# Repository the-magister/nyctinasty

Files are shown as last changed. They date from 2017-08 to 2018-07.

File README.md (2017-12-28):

# Nyctinasty Oasis

Submitting for an Honoraria grant for Burning Man 2018.  An interactive playground celebrating the rhythm of night and day. By day the piece provides climbing fun, shade, and misters powered by movement. At night the lights come on, the sound enlivens and the fire and smoke show begins. The final night, the flower-like structure will wilt and burn.

3D render of Sepal

## Physical Description

Three climbable outriggers around a 32 ft radius circle surround a central flower. 16 ft tall, the outriggers support 20 people dancing and climbing. Built of wood and covered in shade cloth, they feature water misters and hammocks for daytime refuge. Misters are housed in vines, flowers decorate the structure, and leaf-like streamers unfurl overhead.

The center flower is a 16 ft tall metal structure comprised of three metal petals with flame and fog effect heads. Each petal is 3 ft W x 6ft L * 16 ft H. They each have a secured metal base, topped with a foldable rigid origami paneling crafted from 16 gauge metal with metal hinging. A propane accumulator is stored within each petal and plumbed to the tip of the paneling. Each base has 50 meters of RGB LEDs wrapped around the accumulator, diffused by semi-opaque HDPE panels.

## Interactivity and Mission

Nyctinasty Oasis is a day/night playground. Each outrigger is a climbable shade structure. With chill day music, participants can climb the structure, play with it to coax cooling mists, or take a break in the hammocks underneath.
Also incorporated is a sound puzzle, where the participants use movement to mix together multiple tracks of sounds to complete a song. Each outrigger contains three sensor bars which detect the frequency and location of the participants using infrared sensors. The game incorporates collaborative movement to create a coherent whole. Songs composed of three tracks (e.g., bass/melody/vocals) will have each track randomly assigned. As the dancers move and align their tracks, the lights and music will synchronize, rewarding with cooling mists and sounds during the day, and coordinated light at night.

The central flower coordinates with fire and fog. At the end of the week, Nyctinasty Oasis is burned, leaving participants to wonder if it was all a mirage.

## Philosophy

Nyctinasty is the circadian rhythmic movement of plants in response to day and night. An oasis is a fertile habitat found in a desert. Together, a nyctinasty oasis is a retreat that provides both respite and reactivity that changes and is available from day to night. We seek to express how experience varies depending on time of day, point of view, activity level, and community involvement. Nyctinasty Oasis has diurnal features that return upon sunrise and sundown, as well as constant features. During the day, Nyctinasty Oasis provides solace with shade, hammocks, and water misters. Chill, low-volume ambient music is controlled by interaction with the outrigger sensors. At night, the lights come out to play along with a multi-track interactive musical and fire experience that varies based on the number of participants at points along the outriggers. The Nyctinasty Oasis experience is externally guided by regular circadian elements, but also influenced by user participation and determination. The Nyctinasty Oasis also provides constants, a playground standing ready for climbing, hiding, and chilling day or night. We wish to communicate to participants that the experience will be regular, changeable, and replenishing.

## Hardware 

Nyctinasty functions as a distributed set of microcontrollers (uC).  In this sense, the project shares the archetecture of an IoT system.  However, processing is all conducted locally (as opposed to typical cloud-based IoT processing).

### Devices

* Networking: WiFi router, RFM69H(C)W peer-to-peer, FM for sound.
* Wemos D1 Mini (ESP8266): and mainstay microcontroller (uC).
* Arduino Nano (Atmel 328P): analog-to-digitial conversion
* Moteino R3 (Atmel 328P): bridge to legacy HopeRF-mediated peer-to-peer hardware
* Tsunami Super WAV Trigger (ARM Cortex m7): audio generation
* Sharp IR Distance Sensor (GP2Y0A02YK0F): range and motion detection
* Addressable LEDs (WS2811): lighting
* pump (TBD): mister system

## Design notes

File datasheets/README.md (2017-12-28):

Technical details for the devices used in the project.

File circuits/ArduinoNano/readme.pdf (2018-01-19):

### Arduino Nano V3.0 Module for CADSoft EAGLE

### This library was created by Esp. Marco-Luis SALCEDO TOVAR, please report any errors or suggestions to: yv1hx@cantv.net

This version: 0.6 (maintenance release), released on: January 01, 2.017.

### Revision history:

Version | Date | Comments
0.1 | January 22, 2.016 | Initial Release.
0.2 January 25, 2.016 | | Added: Revision history table. Updated: Minor cosmetic changes. Device general description.
0.3 February 05, 2.016 | | Added: Updated signal names labels on most multipurpose pins. Signal directions (Arrows) on D0/RX – D1/TX pins. Updated: Revision history table.
0.4 May 30, 2.016 | | Added: Center cross marks on board corner holes. Updated: Revision history table. Library updated and tested for compatibility on Eagle 7.5.0. Minor cosmetic changes on history table formatting. Updated device physical dimensions on general specifications table.
0.5 August 02, 2.016 | | Added: N/A. Updated: Revision history table. Library updated and tested for compatibility on Eagle 7.6.0.
0.6 January 01, 2.017 | | Added: N/A. Updated: Revision history table. Library updated and tested for compatibility on Eagle 7.7.0.

### Released under the Creative Commons Attribution-ShareAlike 2.5 Generic (CC

BY-SA 2.5) license terms.

### You are free to: Share — copy and redistribute the material in any medium or format Adapt — remix, transform, and build upon the material for any purpose, even

commercially.

### The licensor cannot revoke these freedoms as long as you follow the license

terms.
You can download a full copy of this license from here.

### Thanks for trying my library!

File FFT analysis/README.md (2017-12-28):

Processing the spacial-temporal data into frequency-temporal knowledge isn't trivial.  Each Arch has 8 distance sensors.  Each Sepal has three arches.  Nyctinasty has three Sepals.

From this, we can understand that processing distance data into "coordination" information is non-trivial!

Files in this area are stand-alone (R) applications that are used to develop methods.  Those methods, once sound, get translated to the uC code elsewhere.

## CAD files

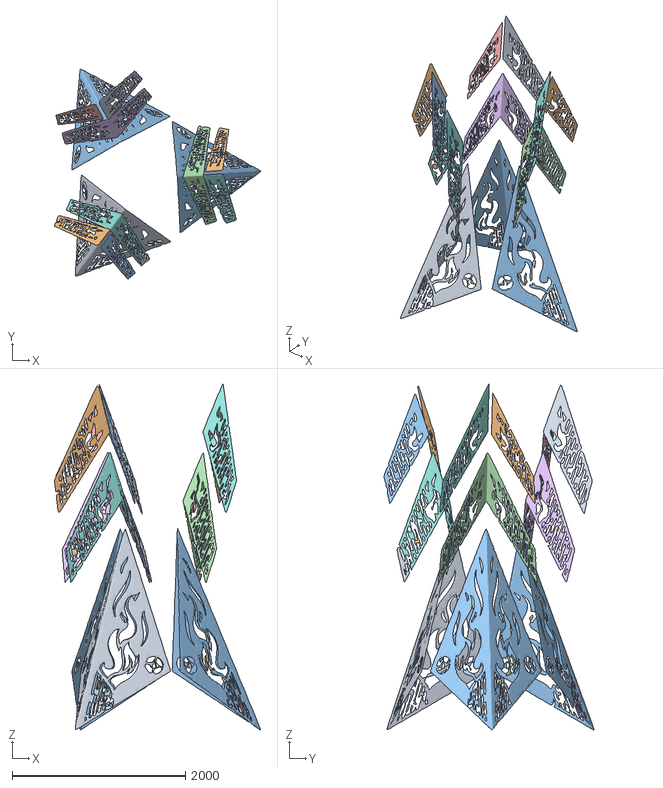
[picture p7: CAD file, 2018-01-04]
processing/sepal_status/application.linux-arm64/data/center - reduced.obj
2377.7 x 2424.0 x 3990.7

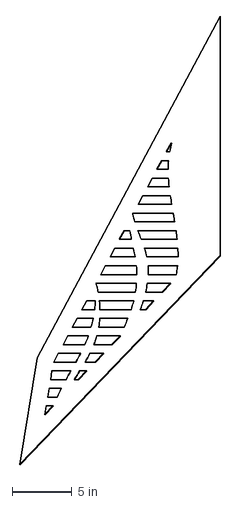
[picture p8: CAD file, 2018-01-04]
processing/sketch_sails/data/sail_A rev 3.DXF
16.8 x 37.6 in

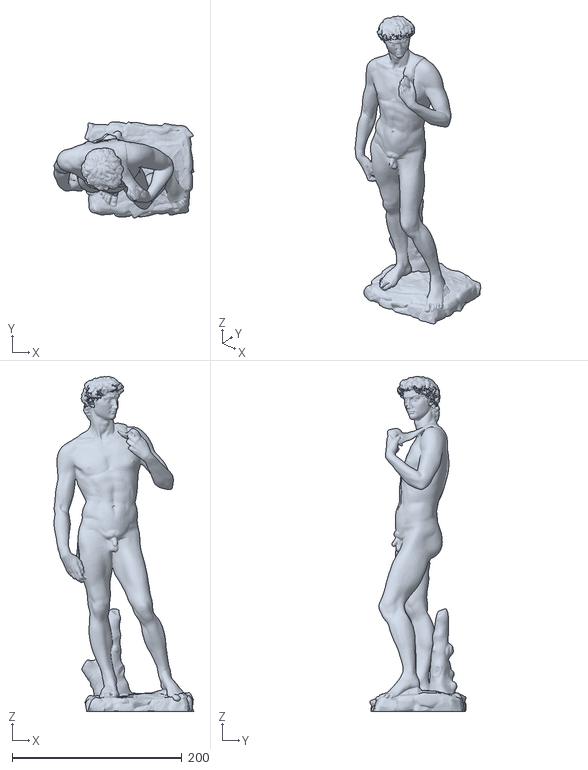
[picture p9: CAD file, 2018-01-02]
processing/sepal_status/application.linux-arm64/data/scan-the-world-michelangelo-s-david - reduced.obj
164.9 x 113.8 x 395.0

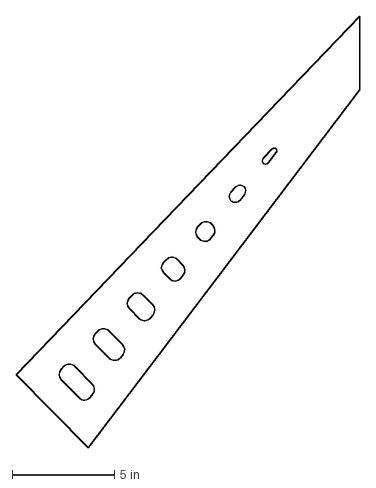
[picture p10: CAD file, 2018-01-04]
processing/sketch_sails/data/sail_B rev 3.DXF
16.8 x 21.1 in

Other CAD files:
processing/sketch_sails/data/sail_C rev 3.DXF
processing/sketch_sails/data/sail_G rev 3.DXF
processing/sketch_sails/data/sail_D rev 3.DXF
processing/sketch_sails/data/sail_E rev 3.DXF
processing/sketch_sails/data/sail_F rev 3.DXF
processing/sketch_sails/data/sail_F_v4.dxf

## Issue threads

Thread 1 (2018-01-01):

Router: bonjour/zeroconf services for OTA programming and *.local name resolution

the-magister, 2018-01-01:
Nyctinasty_Comms library module makes OTA programming via the IDE and name resolution in *.local available via mDNS.  The router is running avachi-daemon and mdns-daemon, so it should "see" the ESP8266 devices.  It doesn't, and I suspect:

- Something in dd-wrt is blocking that announcement/service.  I have tried turning off the firewall.
- Something in DNSmasq could be culprit for *.local lookup.

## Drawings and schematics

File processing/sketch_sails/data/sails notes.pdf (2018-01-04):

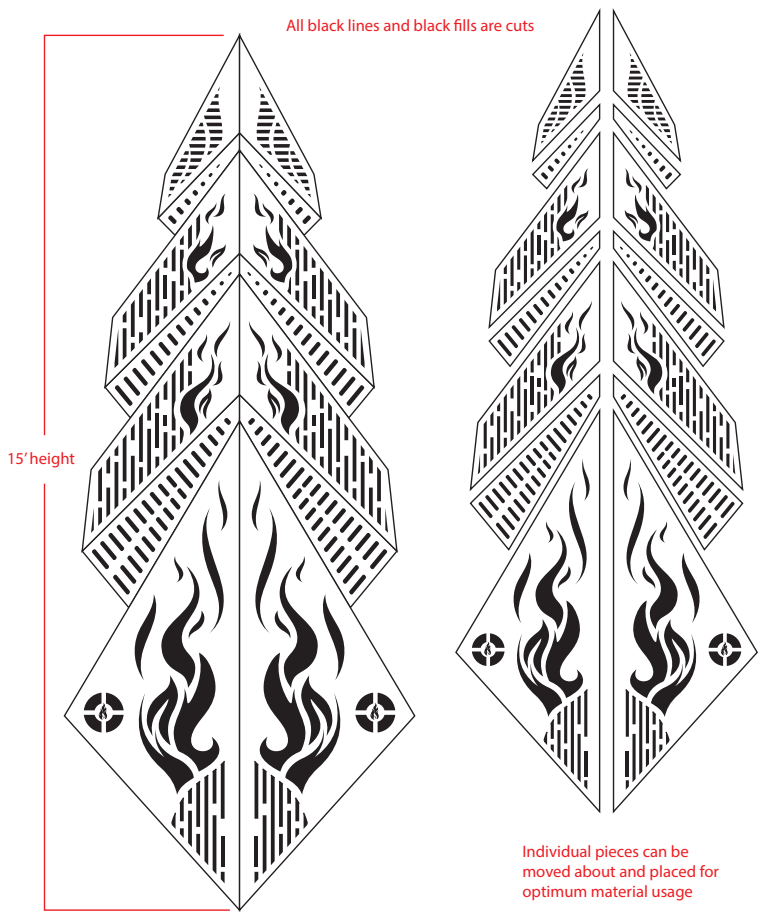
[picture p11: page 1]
15’ height

All black lines and black lls are cuts

Individual pieces can be
moved about and placed for
optimum material usage

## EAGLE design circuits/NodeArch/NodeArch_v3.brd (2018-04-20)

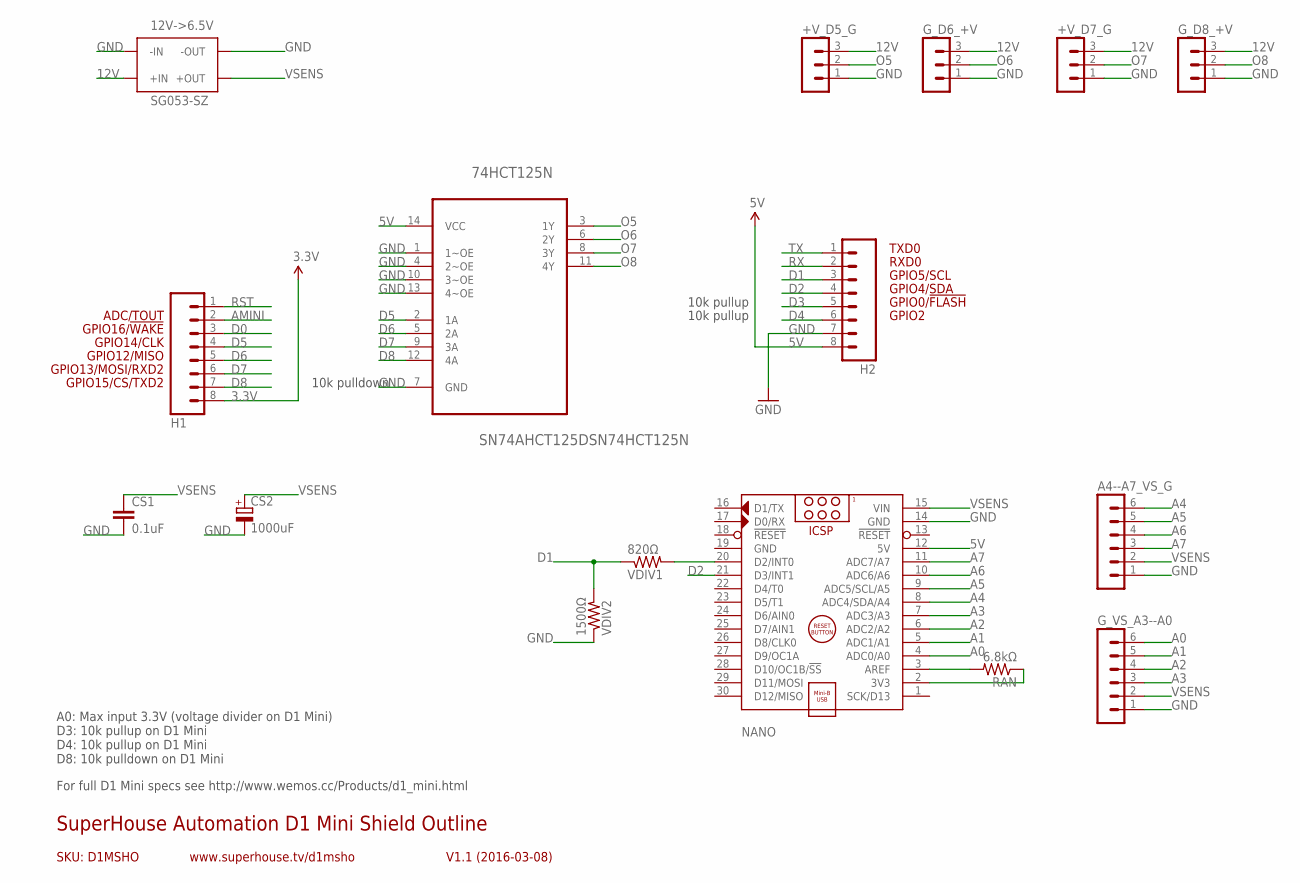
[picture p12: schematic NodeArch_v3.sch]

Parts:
12V->6.5V: SG053-SZ
74HCT125N: SN74AHCT125DSN74HCT125N; DIP254P762X508-14
+V_D5_G, +V_D7_G: MA03-1
A4--A7_VS_G: MA06-1
CS1: 0.1uF; C025-025X050
CS2: 1000uF; E5-10,5
G_D6_+V, G_D8_+V: MA03-1
G_VS_A3--A0: MA06-1
H1, H2: M08; 1X08
NANO: ARDUINO_NANO
RAN: 6.8kΩ; 0207/2V
VDIV1: 820Ω; 0207/2V
VDIV2: 1500Ω; 0207/2V

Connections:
3.3V: H1.8
5V: 74HCT125N.14 (VCC), H2.8, NANO.12 (5V)
12V: 12V->6.5V.P$3 (+IN), 12V->6.5V.P$4 (+IN), +V_D5_G.3, +V_D7_G.3, G_D6_+V.3, G_D8_+V.3
A0: G_VS_A3--A0.6, NANO.4 (ADC0/A0)
A1: G_VS_A3--A0.5, NANO.5 (ADC1/A1)
A2: G_VS_A3--A0.4, NANO.6 (ADC2/A2)
A3: G_VS_A3--A0.3, NANO.7 (ADC3/A3)
A4: A4--A7_VS_G.6, NANO.8 (ADC4/SDA/A4)
A5: A4--A7_VS_G.5, NANO.9 (ADC5/SCL/A5)
A6: A4--A7_VS_G.4, NANO.10 (ADC6/A6)
A7: A4--A7_VS_G.3, NANO.11 (ADC7/A7)
AMINI: H1.2
D0: H1.3
D1: H2.3, VDIV1.1, VDIV2.2
D2: H2.4, NANO.21 (D3/INT1)
D3: H2.5
D4: H2.6
D5: 74HCT125N.2 (1A), H1.4
D6: 74HCT125N.5 (2A), H1.5
D7: 74HCT125N.9 (3A), H1.6
D8: 74HCT125N.12 (4A), H1.7
GND: 12V->6.5V.P$1 (-IN), 12V->6.5V.P$2 (-IN), 12V->6.5V.P$7 (-OUT), 12V->6.5V.P$8 (-OUT), 74HCT125N.1 (1~OE), 74HCT125N.4 (2~OE), 74HCT125N.7 (GND), 74HCT125N.10 (3~OE), 74HCT125N.13 (4~OE), +V_D5_G.1, +V_D7_G.1, A4--A7_VS_G.1, CS1.2, CS2.-, G_D6_+V.1, G_D8_+V.1, G_VS_A3--A0.1, H2.7, NANO.14 (GND), NANO.19 (GND), VDIV2.1
unnamed: NANO.3 (AREF), RAN.2
unnamed: NANO.2 (3V3), RAN.1
unnamed: NANO.20 (D2/INT0), VDIV1.2
O5: 74HCT125N.3 (1Y), +V_D5_G.2
O6: 74HCT125N.6 (2Y), G_D6_+V.2
O7: 74HCT125N.8 (3Y), +V_D7_G.2
O8: 74HCT125N.11 (4Y), G_D8_+V.2
RST: H1.1
RX: H2.2
TX: H2.1
VSENS: 12V->6.5V.P$5 (+OUT), 12V->6.5V.P$6 (+OUT), A4--A7_VS_G.2, CS1.1, CS2.+, G_VS_A3--A0.2, NANO.15 (VIN)

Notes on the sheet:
GPIO2
GPIO0/!FLASH
GPIO12/MISO
GPIO4/SDA
GPIO5/SCL
RXD0
TXD0
GPIO13/MOSI/RXD2
GPIO14/CLK
GPIO15/CS/TXD2
GPIO16/!WAKE
SKU: D1MSHO
SuperHouse Automation D1 Mini Shield Outline
V1.1 (2016-03-08)
www.superhouse.tv/d1msho
ADC/TOUT
A0: Max input 3.3V (voltage divider on D1 Mini) D3: 10k pullup on D1 Mini D4: 10k pullup on D1 Mini D8: 10k pulldown on D1 Mini
10k pulldown
10k pullup
For full D1 Mini specs see http://www.wemos.cc/Products/d1_mini.html

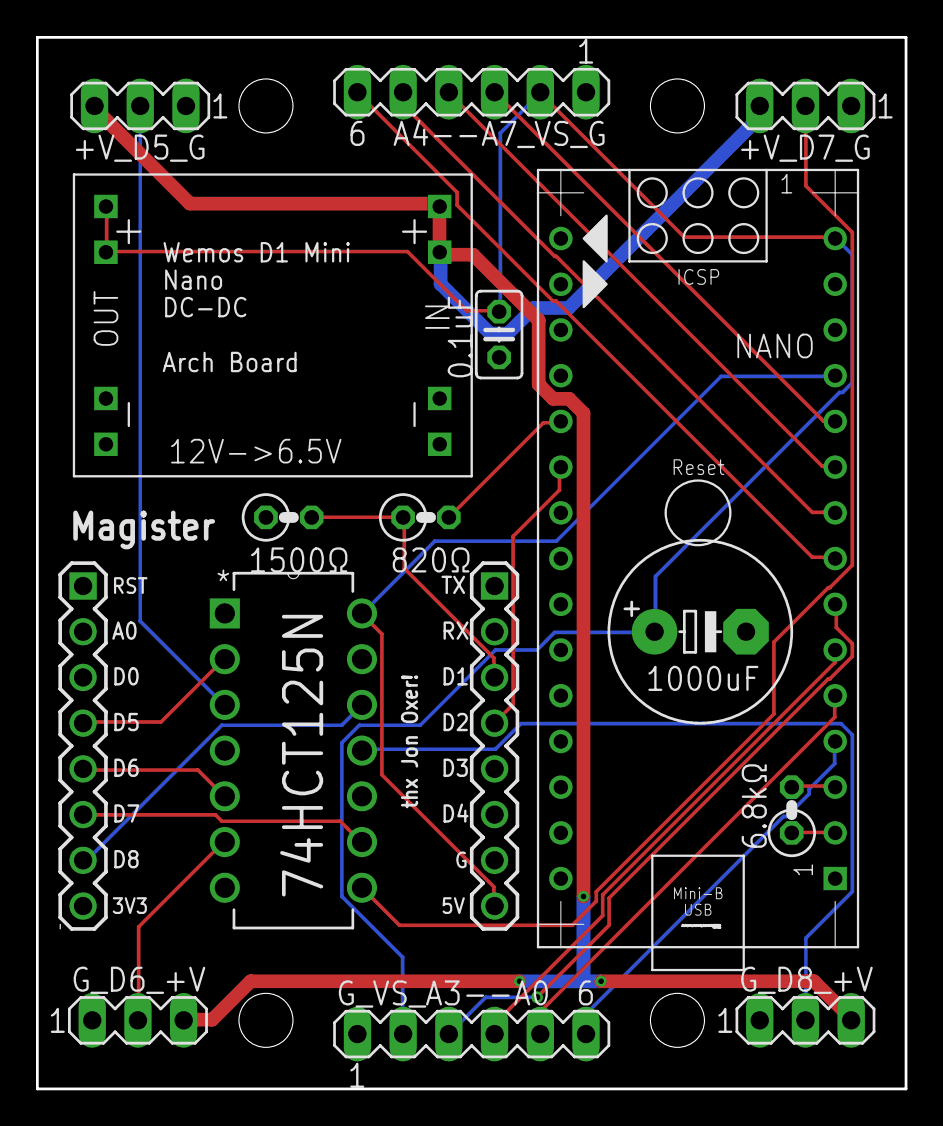
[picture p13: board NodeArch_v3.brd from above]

Board: 2 copper layers, 48.3 x 58.4 mm, 16 parts (0 on the bottom side), 25 nets.

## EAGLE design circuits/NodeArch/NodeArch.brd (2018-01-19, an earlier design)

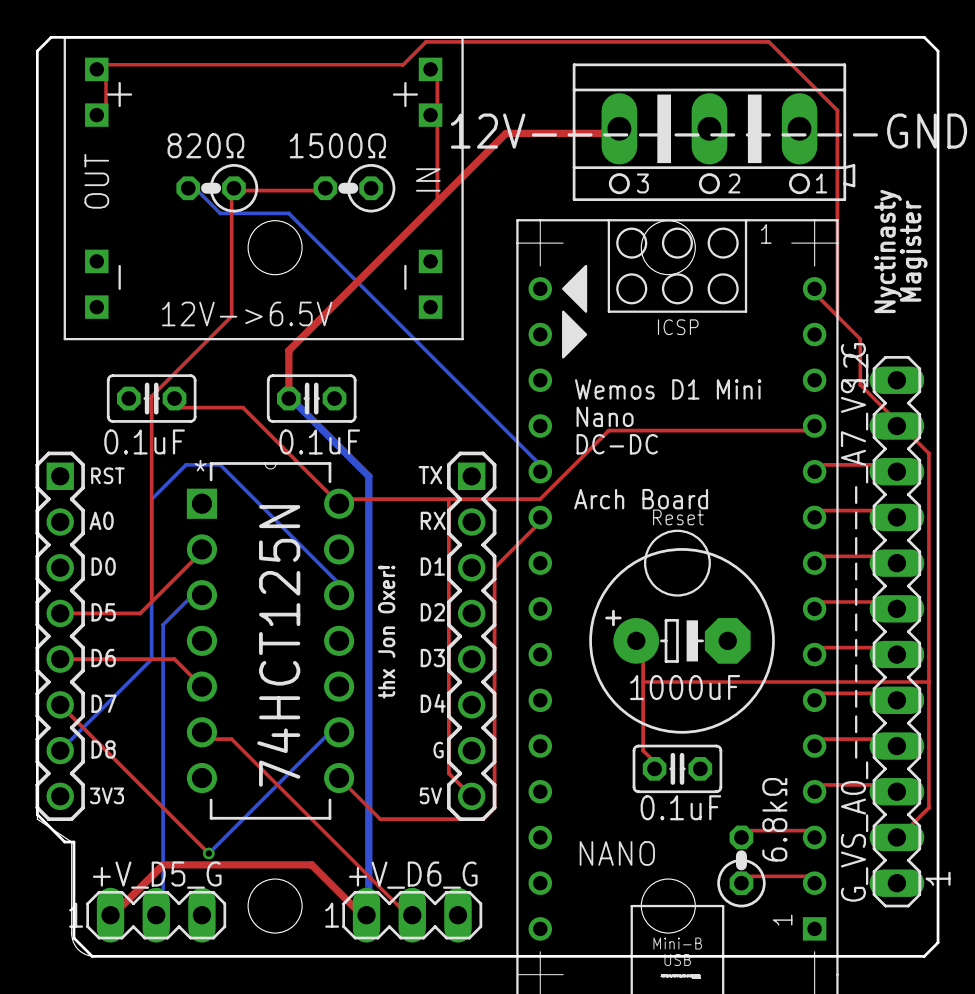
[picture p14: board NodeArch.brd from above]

Board: 2 copper layers, 50.0 x 51.1 mm, 16 parts (0 on the bottom side), 22 nets.

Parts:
12V----------GND: AK500/3
12V->6.5V: SG053-SZ
74HCT125N: SN74AHCT125DSN74HCT125N; DIP254P762X508-14
+V_D5_G, +V_D6_G: MA03-1
C5, C12: 0.1uF; C025-025X050
CS1: 0.1uF; C025-025X050
CS2: 1000uF; E5-10,5
G_VS_A0_-----------_A7_VS_G: MA12-1
H1, H2: 1X08
NANO: ARDUINO_NANO
RAN: 6.8kΩ; 0207/2V
VDIV1: 820Ω; 0207/2V
VDIV2: 1500Ω; 0207/2V

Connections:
5V: 74HCT125N.14, C5.1, H2.8, NANO.12
12V: 12V----------GND.3, 12V->6.5V.P$3, 12V->6.5V.P$4, +V_D5_G.1, +V_D6_G.1, C12.1
A0: G_VS_A0_-----------_A7_VS_G.3, NANO.4
A1: G_VS_A0_-----------_A7_VS_G.4, NANO.5
A2: G_VS_A0_-----------_A7_VS_G.5, NANO.6
A3: G_VS_A0_-----------_A7_VS_G.6, NANO.7
A4: G_VS_A0_-----------_A7_VS_G.7, NANO.8
A5: G_VS_A0_-----------_A7_VS_G.8, NANO.9
A6: G_VS_A0_-----------_A7_VS_G.9, NANO.10
A7: G_VS_A0_-----------_A7_VS_G.10, NANO.11
D5: 74HCT125N.2, H1.4, VDIV1.1, VDIV2.2
D6: 74HCT125N.5, H1.5
D7: 74HCT125N.9, H1.6
D8: 74HCT125N.12, H1.7
GND: 12V----------GND.1, 12V----------GND.2, 12V->6.5V.P$1, 12V->6.5V.P$2, 12V->6.5V.P$7, 12V->6.5V.P$8, 74HCT125N.1, 74HCT125N.4, 74HCT125N.7, 74HCT125N.10, 74HCT125N.13, +V_D5_G.3, +V_D6_G.3, C5.2, C12.2, CS1.2, CS2.-, G_VS_A0_-----------_A7_VS_G.1, G_VS_A0_-----------_A7_VS_G.12, H2.7, NANO.14, NANO.19, VDIV2.1
unnamed: NANO.3, RAN.2
unnamed: NANO.2, RAN.1
O5: 74HCT125N.3, +V_D5_G.2
O6: 74HCT125N.6, +V_D6_G.2
O7: 74HCT125N.8, NANO.21
TXAVR: NANO.20, VDIV1.2
VSENS: 12V->6.5V.P$5, 12V->6.5V.P$6, CS1.1, CS2.+, G_VS_A0_-----------_A7_VS_G.2, G_VS_A0_-----------_A7_VS_G.11, NANO.15

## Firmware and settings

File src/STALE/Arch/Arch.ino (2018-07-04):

// IDE Settings:
// Tools->Board : "WeMos D1 R2 & mini"
// Tools->Flash Size : "4M (3M SPIFFS)"
// Tools->CPU Frequency : "160 MHz"
// Tools->Upload Speed : "921600"

#include <Streaming.h>
#include <Metro.h>
#include <arduinoFFT.h>
#include <SoftwareSerial.h>
#include <SoftEasyTransfer.h>
#include <FiniteStateMachine.h>
#define FASTLED_INTERRUPT_RETRY_COUNT 1
#include <FastLED.h>
#include "Nyctinasty_Messages.h"
#include "Nyctinasty_Comms.h"

// spammy?
#define SHOW_SERIAL_DEBUG true

// my role and arch number
NyctRole myRole = N_ROLES; // see Nyctinasty_Comms.h; set N_ROLES to pull from EEPROM
// Arch0, Arch1, Arch2 for bootstrapping a new controller.
byte myArch;
byte leftArch, rightArch;
byte leftCoord, rightCoord;

// wire it up
#define RX D1 // GPIO5
#define TX D2 // GPIO4 
// voltage divider: 5V->3.3V
// TX to RX_ESP via 820 Ohm resistor
// RX_ESP to GND via 1500 Ohm resistor
// LEDs are connected:
// D5, GPIO14
// D6, GPIO12
// D7, GPIO13
// D8, GPIO15
// also used
// D4, GPIO2, BUILTIN_LED

// LED handling

// our internal storage, mapped to the hardware.
// pay no attention to the man behind the curtain.
#define COLOR_ORDER RGB
#define COLOR_CORRECTION TypicalLEDStrip
#define NUM_PINS 4
#define LEDS_BAR 3
#define LEDS_DOWN 17
#define LEDS_UP 13
#define LEDS_DECK 4
#define LEDS_PER_PIN LEDS_BAR+LEDS_DOWN

CRGBArray<LEDS_PER_PIN> leftBack;
CRGBArray<LEDS_PER_PIN> rightBack;
CRGBArray<LEDS_PER_PIN> leftFront;
CRGBArray<LEDS_PER_PIN> rightFront;

// bars
CRGBSet rightBar1 = rightBack(0, LEDS_BAR-1);
CRGBSet rightBar2 = rightFront(0, LEDS_BAR-1);
CRGBSet leftBar1 = leftBack(0, LEDS_BAR-1);
CRGBSet leftBar2 = leftFront(0, LEDS_BAR-1);

// verticals
CRGBSet leftUp = leftFront(LEDS_BAR, LEDS_UP-1);
CRGBSet rightUp = rightFront(LEDS_BAR, LEDS_UP-1);
CRGBSet leftDown = leftBack(LEDS_BAR, LEDS_DOWN-1);
CRGBSet rightDown = rightBack(LEDS_BAR, LEDS_DOWN-1);

// deck lights under rail
CRGBSet leftDeck = leftUp(LEDS_BAR+LEDS_UP, LEDS_PER_PIN-1);
CRGBSet rightDeck = rightUp(LEDS_BAR+LEDS_UP, LEDS_PER_PIN-1);

// color choices, based on arch information
const CHSV archColor[N_ARCH] = {
  CHSV(HUE_RED, 255, 255),
  CHSV(HUE_GREEN, 255, 255),
  CHSV(HUE_BLUE, 255, 255)
};

// deck lighting
CRGB deckColor = CRGB::FairyLight;

// comms
NyctComms comms;

// define a state for every systemState
void startup(); State Startup = State(startup);
void lonely(); State Lonely = State(lonely);
void ohai(); State Ohai = State(ohai);
void goodnuf(); State Goodnuf = State(goodnuf);
void goodjob(); State Goodjob = State(goodjob);
void winning(); State Winning = State(winning);
void fanfare(); State Fanfare = State(fanfare);
void reboot() { comms.reboot(); }; State Reboot = State(reboot);
FSM stateMachine = FSM(Startup); // initialize state machine

// incoming message storage and flag for update
struct sC_t {
  boolean hasUpdate = false;
  SystemCommand settings;
} sC;

// our distance updates send as this structure as this topic
const uint32_t distancePublishRate = 1000UL/15UL; // ms
SepalArchDistance dist;

// our frequency updates send as this structure as this topic
// other frequency updates receive as this structure as this topic
typedef struct {
  boolean hasUpdate = false;
  SepalArchFrequency freq;
} sAF_t;
sAF_t sAF[N_ARCH];

// FFT object
uint16_t buffer[N_SENSOR][N_FREQ_SAMPLES];
boolean bufferReady = false;
arduinoFFT FFT = arduinoFFT();

// computed correspondence [-1,+1] between arches.
float concordTotal, concordNext, concordPrev;

// talk to the ADC device
SoftwareSerial mySerial(RX, TX, false, 1024);
SoftEasyTransfer ETin;

void setup() {
  // for local output
  Serial.begin(115200);

  Serial << endl << endl << endl << F("Startup begins.") << endl;

  // for remote output
  Serial << F("Configure softwareserial...");
  mySerial.begin(115200);
  // messages
  ETin.begin(details(dist), &mySerial);
  // after set up the input pin
  pinMode(TX, OUTPUT); // trigger to send
  Serial << F(" done.") << endl;

  // LEDs
  Serial << F("Configure leds...");
  FastLED.addLeds<WS2811, D5, COLOR_ORDER>(leftBack, LEDS_PER_PIN).setCorrection(COLOR_CORRECTION);
  FastLED.addLeds<WS2811, D6, COLOR_ORDER>(rightBack, LEDS_PER_PIN).setCorrection(COLOR_CORRECTION);
  FastLED.addLeds<WS2811, D7, COLOR_ORDER>(leftFront, LEDS_PER_PIN).setCorrection(COLOR_CORRECTION);
  FastLED.addLeds<WS2811, D8, COLOR_ORDER>(rightFront, LEDS_PER_PIN).setCorrection(COLOR_CORRECTION);
  FastLED.setBrightness(255);
  Serial << F(" done.") << endl;

  // configure comms
  comms.begin(myRole);
  myRole = comms.getRole();
  myArch = myRole - 1;
  switch(myArch) {
    case 0: 
      // sC.isPlayer indexes
      leftArch=1; rightArch=2; 
      // sC.areCoordinated indexes
      leftCoord=0; rightCoord=2;
      break;
    case 1: 
      leftArch=2; rightArch=0; 
      leftCoord=1; rightCoord=0;
      break;
    case 2: 
      leftArch=0; rightArch=1; 
      leftCoord=2; rightCoord=1;
      break;    
  }
  Serial << F("Arch indexes: left=") << leftArch << F(" my=") << myArch << F(" right=") << rightArch << endl;
  Serial << F("Coordination indexes: left=") << leftCoord << F(" right=") << rightCoord << endl;
  
  // subscribe
  comms.subscribe(&sC.settings, &sC.hasUpdate);
  for ( byte a = 0; a < N_ARCH; a++ ) {
    // no need to subscribe to our own message
    if ( a != myArch ) comms.subscribe(&sAF[a].freq, &sAF[a].hasUpdate, a);
  }

  Serial << F("DISTANCE_SAMPLING_RATE, ms: ") << DISTANCE_SAMPLING_RATE << endl;
  Serial << F("DISTANCE_SAMPLING_FREQ, Hz: ") << DISTANCE_SAMPLING_FREQ << endl;
  Serial << F("N_FREQ_SAMPLES, #: ") << N_FREQ_SAMPLES << endl;
  Serial << F("FILL_TIME, ms: ") << FILL_TIME << endl;
  Serial << F("Lowest Freq Bin, Hz: ") << (float)(0+1)*(float)DISTANCE_SAMPLING_FREQ/(float)N_FREQ_SAMPLES << endl;
  Serial << F("Highest Freq Bin, Hz: ") << (float)(N_FREQ_BINS+1)*(float)DISTANCE_SAMPLING_FREQ/(float)N_FREQ_SAMPLES << endl;

  Serial << F("Startup complete.") << endl;
}

void loop() {
  // comms handling
  comms.update();

/*
  // after 5 seconds, transition to Offline, but we could easily get directed to Online before that.
  static Metro cycleTimeout(5000UL);
  if( cycleTimeout.check() ) {
    sC.settings.state = (systemState)((int)sC.settings.state+1);
    if( sC.settings.state == REBOOT ) sC.settings.state = STARTUP;
    sC.hasUpdate = true;
    cycleTimeout.reset();
  }
*/

  // check for settings update
  if ( sC.hasUpdate ) {
    updateState();
    calculateCoordPalette();
    calculatePlayerPalette();
    sC.hasUpdate = false;
  }

  // do stuff
  stateMachine.update();

  // update the sensor data
  updateSensors();
}

CRGBPalette16 coordPalette;
void calculateCoordPalette() {
  
  CRGBArray<16> pal;
  
  if( sC.settings.areCoordinated[leftCoord] ) {
    pal.fill_gradient(archColor[leftArch], archColor[myArch], archColor[leftArch] );
  } else {
    pal = CRGB::Black;
  }
  if( sC.settings.areCoordinated[rightCoord] ) {
    pal.fill_gradient(archColor[rightArch], archColor[myArch], archColor[rightArch] );
  } else {
    pal = CRGB::Black;
  }

  // copy out
  for(byte i=0; i<16; i++) coordPalette[i] = pal[i];
}

CRGBPalette16 playerPaletteLeft, playerPaletteRight; // left, right
void calculatePlayerPalette() {
  
  CHSV me = CHSV(archColor[myArch].hue, archColor[myArch].sat, 
    sC.settings.isPlayer[myArch] ? 255 : 0
  );
  CHSV left = CHSV(archColor[leftArch].hue, archColor[leftArch].sat, 
    sC.settings.isPlayer[leftArch] ? 255 : 0
  );
  CHSV right = CHSV(archColor[rightArch].hue, archColor[rightArch].sat, 
    sC.settings.isPlayer[rightArch] ? 255 : 0
  );

  CRGBArray<16> palLeft;
  palLeft.fill_gradient(left, me, left);

  CRGBArray<16> palRight;
  palRight.fill_gradient(right, me, right);
 
  // copy out
  for(byte i=0; i<16; i++) {
    playerPaletteLeft[i] = palLeft[i];
    playerPaletteRight[i] = palRight[i];
  }
}


void updateState() {

  switch ( sC.settings.state ) {
    case STARTUP: stateMachine.transitionTo(Startup); break;
    case LONELY: stateMachine.transitionTo(Lonely); break;
    case OHAI: stateMachine.transitionTo(Ohai); break;
    case GOODNUF: stateMachine.transitionTo(Goodnuf); break;
    case GOODJOB: stateMachine.transitionTo(Goodjob); break;
    case WINNING: stateMachine.transitionTo(Winning); break;
    case FANFARE: stateMachine.transitionTo(Fanfare); break;
    case REBOOT: stateMachine.transitionTo(Reboot); break;
    default:
      Serial << F("ERROR!  unknown state.") << endl;
  }

  Serial << F("State change. to=");
  switch( sC.settings.state ) {
    case STARTUP: Serial << "STARTUP"; break;  //  all roles start here
  
    case LONELY: Serial << "LONELY"; break;   // 0 players
    case OHAI: Serial << "OHAI"; break;   // 1 players
    case GOODNUF: Serial << "GOODNUF"; break;  // 2 players
    case GOODJOB: Serial << "GOODJOB"; break;  // 3 players or 2 players coordinated
    case WINNING: Serial << "WINNING"; break;  // 3 players and 2 players coordinated
    case FANFARE: Serial << "FANFARE"; break;  // 3 players and 3 players coordinated 
  
    case REBOOT: Serial << "REBOOT"; break;   //  trigger to reboot 
  }
  Serial << ". isPlayer? A0=" << sC.settings.isPlayer[0];
  Serial << " A1=" << sC.settings.isPlayer[1];
  Serial << " A2=" << sC.settings.isPlayer[2];
  Serial << ". coord? A01=" << sC.settings.areCoordinated[0];
  Serial << " A12=" << sC.settings.areCoordinated[1];
  Serial << " A20=" << sC.settings.areCoordinated[2];
  Serial << endl;

}

void startup() {
  
  static byte hue = archColor[myArch].hue;
  EVERY_N_MILLISECONDS(10) {
    // show a throbbing rainbow background
    hue++;
    leftUp.fill_rainbow(hue, 255 / leftUp.size()); // paint
    rightUp = leftUp;
    leftDown.fill_rainbow(hue + 128, -255 / leftDown.size());
    rightDown = leftFront;
    
    // color the bar with our color
    leftBar1.fill_solid(archColor[myArch]);
    rightBar2 = rightBar1 = leftBar2 = leftBar1;
    
    // do it now
    pushToHardware();
  }

}

void lonely() {
  // need some kind of "walk into the arches" animation
  playerAndCoordinationUpdate();
}

void ohai() {
  playerAndCoordinationUpdate();
}

void goodnuf() {
  playerAndCoordinationUpdate();
}

void goodjob() {
  playerAndCoordinationUpdate();
}

void winning() {
  playerAndCoordinationUpdate();
}

void fanfare() {
  // need some kind of "yeah, playah!" animation
  playerAndCoordinationUpdate();
}

void playerAndCoordinationUpdate() {
  updateDeck();
  updateTopsByCoordination();
  updateLegsByPlayer();
}

void updateDeck() {
  leftDeck.fill_solid(deckColor);
  rightDeck.fill_solid(deckColor);
}

void updateTopsByCoordination() {
  static byte colorIndex = 0;  
  
  EVERY_N_MILLISECONDS( 20 ) {
    colorIndex ++;
    byte j = 0;
    for ( int i = 0; i < leftUp.size(); i++) {
      leftUp[i] = ColorFromPalette( coordPalette, colorIndex + j++, 255, LINEARBLEND );
    }
    j = 0;
    for ( int i = 0; i < rightUp.size(); i++) {
      rightUp[i] = ColorFromPalette( coordPalette, colorIndex + j++, 255, LINEARBLEND );
    }
  }  
}

void updateLegsByPlayer() {
  static byte colorIndex = 0;
  
  EVERY_N_MILLISECONDS( 20 ) {
    colorIndex ++;
    byte j = 0;
    for ( int i = 0; i < leftDown.size(); i++) {
      leftDown[i] = ColorFromPalette( playerPaletteLeft, colorIndex + j++, 255, LINEARBLEND );
    }
    j = 0;
    for ( int i = 0; i < rightDown.size(); i++) {
      rightDown[i] = ColorFromPalette( playerPaletteRight, colorIndex + j++, 255, LINEARBLEND );
    }
  }  

}

void updateSensors() {

/*
 * Order of operation is critical here.  We have three subsystems that use ISRs:
 *  FastLED: turns off ISRs
 *  WiFi: received information may be lost w/o ISR
 *  SoftwareSerial: received information may be lost w/o ISR
 *  
 *  From this, you can see that we need to be very careful with FastLED.show(), and 
 *  queue those up after we get SoftwareSerial data.  Can't really control when we get
 *  WiFi packets.
 *
 */
 
 static uint32_t counter = 0;
  static boolean publishReady = false;
  static byte fftIndex = 0;
  static Metro pushDistanceInterval(distancePublishRate);

  // do FFT in segements when the buffer is ready
  if ( bufferReady ) {
    // compute
    computeFFT(fftIndex);

    // next sensor
    fftIndex++;

    // are we done?
    if ( fftIndex >= N_SENSOR ) {
      fftIndex = 0;
      bufferReady = false;
      publishReady = true;
    }
  }

  // check to see if we need to pull new distance data.
  // toggled TX pin
  static boolean pinState = false;
  static Metro distanceUpdate(DISTANCE_SAMPLING_RATE);

  if ( distanceUpdate.check() ) {
    distanceUpdate.reset();
    pinState = !pinState;
    digitalWrite(TX, pinState);
  }

  // get data from ADCs
  if ( ETin.receiveData() ) {
    // just tracking actual distance update rate
    counter ++;

    // fill buffer
    fillBuffer();

    // update bar lights
    updateBarByDistance();

    // I don't actually know if sending via WiFi will disrupt SoftwareSerial; worth a look.
    if ( publishReady ) {
      publishReady = false;
      // publish
      comms.publish(&sAF[myArch].freq, myArch);
      // flag that our frequency data are ready
      sAF[myArch].hasUpdate = true;
    } else if( pushDistanceInterval.check() ) {
      // publish distance
      comms.publish(&dist, myArch);
      pushDistanceInterval.reset();
    }

    // we need to update the LEDs now while we won't screw up SoftwareSerial and WiFi
    pushToHardware();
  }

  const uint32_t reportInterval = 10;
  EVERY_N_SECONDS( reportInterval ) {
    uint32_t actualDISTANCE_SAMPLING_RATE = (reportInterval*1000UL)/counter;

    Serial << F("Distance sample interval, actual=") << actualDISTANCE_SAMPLING_RATE;
    Serial << F(" hypothetical=") << DISTANCE_SAMPLING_RATE;
    Serial << F(" ms.") << endl;
    
    counter=0;
  }
  
}

// adjust lights on the bar with distance readings
void updateBarByDistance() {

  // compute using a dummy set of LEDs
  static CRGBArray<N_SENSOR> bar;
  for ( byte s = 0; s < N_SENSOR; s++ ) {
    // quash noise
    if ( dist.prox[s] < dist.noise ) dist.prox[s] = dist.min;
    uint16_t intensity = map(
                           dist.prox[s],
                           dist.min, dist.max,
                           (uint16_t)0, (uint16_t)255
                         );
    bar[s] = CHSV(archColor[myArch].hue, archColor[myArch].sat, (byte)intensity);
  }

  // assign to hardware. ugly and direct, but we can see what's going on.
  leftBack[2] = leftFront[2] = bar[0];
  leftBack[1] = leftFront[1] = bar[1];
  leftBack[0] = leftFront[0] = bar[2];

  rightBack[0] = rightFront[0] = bar[3];
  rightBack[1] = rightFront[1] = bar[4];
  rightBack[2] = rightFront[2] = bar[5];
}

// adjust lights on the down/legs with frequency readings
void updateLegsByFrequency() {
  // crappy
  uint16_t avgPower[N_SENSOR] = {0};
  // frequency power
  uint16_t power[N_SENSOR][N_FREQ_BINS] = {{0.0}};

  // do the boneheaded thing and sum up the bins across all sensors
  uint32_t sumSensors[N_FREQ_BINS] = {0};
  uint32_t maxSum = 0;
  for ( uint16_t b = 0; b < N_FREQ_BINS ; b++ ) {
    for ( byte s = 0; s < N_SENSOR; s++ ) {
      sumSensors[b] += sAF[myArch].freq.power[s][b];
    }
    if ( sumSensors[b] > maxSum ) maxSum = sumSensors[b];
  }

  Serial << F("Freq bins: ");
  // set the LEDs proportional to bins, normalized to maximum bin
  for ( uint16_t b = 0; b < N_FREQ_BINS ; b++ ) {
    uint32_t value = map( sumSensors[b],
                          (uint32_t)0, maxSum,
                          (uint32_t)0, (uint32_t)255
                        );
    Serial << value << ",";
    leftDown[b] = CHSV(archColor[myArch].hue, archColor[myArch].sat, brighten8_video(constrain(value, 0, 255)));
  }
  Serial << endl;

  rightDown = leftDown;
}

// adjust lights on down/legs with peak frequency readings
void updateLegsByPeakFreq() {

  // some constants
  // maximum possible frequency bin
  const byte maxFreq = ceil( (N_FREQ_BINS+1)*DISTANCE_SAMPLING_FREQ/N_FREQ_SAMPLES );
  const byte minFreq = floor( (0+1)*DISTANCE_SAMPLING_FREQ/N_FREQ_SAMPLES );
  const byte fadeEachUpdate = 128;
  
  // fade lighting
  leftDown.fadeToBlackBy( fadeEachUpdate );

  // loop across each arch's information
  for( byte a=0; a<N_ARCH; a++ ) {
    // loop across each sensor
    for( byte s=0; s<N_SENSOR; s++ ) {
      // get the integer frequency above and below
      byte roundUp = ceil(sAF[a].freq.peakFreq[s]);
      byte roundDown = floor(sAF[a].freq.peakFreq[s]);
      
      // map to lighting position
      byte lightUp = map(roundUp, minFreq, maxFreq, 0, LEDS_UP-1);
      byte lightDown = map(roundDown, minFreq, maxFreq, 0, LEDS_DOWN-1);
      
      // pick a color; my color is the brightest.
      byte bright = 128;
      if( a == myArch ) bright = 255;
      CHSV color = CHSV(archColor[a].hue, 255, bright );

      // apply
      leftDown[lightUp] += color;
      leftDown[lightDown] += color;
    }
    
  }

  // What immortal hand or eye / Could frame thy fearful symmetry?
  rightDown = leftDown;
}

// update lights on the up/overhead with concordance readings
void updateTopsByConcordance() {
  // NOP
}

// show
void pushToHardware() {
  FastLED.show();

  // show our frame rate, periodically
  EVERY_N_SECONDS( 20 ) {
    uint16_t reportedFPS = FastLED.getFPS();
    Serial << F("FastLED reported FPS, Hz=") << reportedFPS << endl;
  }
}

// storage
void fillBuffer() {
  // track the buffer index
  static uint16_t index = 0;

  // push to buffer
  for ( byte i = 0; i < N_SENSOR; i++ ) buffer[i][index] = dist.prox[i];

  // increment buffer index
  index++;

  if ( index >= N_FREQ_SAMPLES ) {
    index = 0;
    bufferReady = true;
  }
}

// show sensor readings
void dumpBuffer(uint16_t count) {
  const char sep = ',';

  for ( uint16_t j = 0; j < N_FREQ_SAMPLES; j++) {
    for ( uint16_t i = 0; i < N_SENSOR; i++ ) {
      Serial << (uint16_t)buffer[i][j] << sep;
    }
    Serial << count << endl;
  }
  count ++;
}

// frequency calculations readings
void dumpFFT() {
  const char sep = ',';
  unsigned long now = millis();

  for ( uint16_t i = 0; i < N_SENSOR; i++ ) {
    Serial << now << sep << i << sep << sAF[myArch].freq.avgPower[i];
    for ( uint16_t j = 0; j < N_FREQ_BINS ; j++ ) {
      Serial << sep << sAF[myArch].freq.power[i][j];
    }
    Serial << endl;
  }
}


// https://cdn-learn.adafruit.com/downloads/pdf/fft-fun-with-fourier-transforms.pdf
// Nyquist's Sampling Theorem: only frequencies up to half the sampling rate can
// can be detected.  So, for 33 fps (Hz) we can detect signals no faster than 33/2 Hz.
/*
  Finally, the output of the FFT on real data has a few interesting properties:
    The very first bin (bin zero) of the FFT output represents the average power of the signal.
  Be careful not to try interpreting this bin as an actual frequency value!
   Only the first half of the output bins represent usable frequency values. This means the
  range of the output frequencies detected by the FFT is half of the sample rate. Don't try to
  interpret bins beyond the first half in the FFT output as they won't represent real frequency
  values!
*/
double imag[N_FREQ_SAMPLES];
double real[N_FREQ_SAMPLES];
#define SCL_INDEX 0x00
#define SCL_TIME 0x01
#define SCL_FREQUENCY 0x02
void computeFFT(byte index) {
  // track time
  unsigned long tic = millis();

  // crunch the buffer; expensive
  const uint8_t exponent = FFT.Exponent(N_FREQ_SAMPLES); // can precompute to save a little time.

  // storage.  fft computations alter the buffer, so we copy
  for ( uint16_t j = 0; j < N_FREQ_SAMPLES ; j++ ) {
    real[j] = (double)buffer[index][j];
    imag[j] = 0.0;
  }

  // weigh data
  FFT.Windowing(real, N_FREQ_SAMPLES, FFT_WIN_TYP_HAMMING, FFT_FORWARD);  /* Weigh data */
  //    Serial.println("Weighed data:"); PrintVector(real, N_FREQ_SAMPLES, SCL_TIME);

  // compute FFT
  FFT.Compute(real, imag, N_FREQ_SAMPLES, exponent, FFT_FORWARD); /* Compute FFT */
  //    Serial.println("Computed Real values:"); PrintVector(real, N_FREQ_SAMPLES, SCL_INDEX);
  //    Serial.println("Computed Imaginary values:"); PrintVector(imag, N_FREQ_SAMPLES, SCL_INDEX);

  // compute magnitudes
//  FFT.ComplexToMagnitude(real, imag, N_FREQ_SAMPLES); /* Compute magnitudes */
  // stealing a march here, as we don't need the magnitude information for the latter
  // half of the array
  FFT.ComplexToMagnitude(real, imag, N_FREQ_BINS + 2); /* Compute magnitudes */
//  Serial.println("Computed magnitudes:");  PrintVector(real, (N_FREQ_SAMPLES >> 1), SCL_FREQUENCY);

  // find major frequency peak
  double peakFreq = FFT.MajorPeak(real, N_FREQ_SAMPLES, DISTANCE_SAMPLING_FREQ);
//  if( index==5 ) Serial << F("Peak: ") << x << endl;
  
  // store power magnitudes of the lowest N_FREQ_BINS in the spectra
  sAF[myArch].freq.avgPower[index] = (uint16_t)real[0];
  for ( uint16_t j = 0; j < N_FREQ_BINS ; j++ ) sAF[myArch].freq.power[index][j] = (uint16_t)real[j + 1];

  // store peak frequency
  sAF[myArch].freq.peakFreq[index] = (float)peakFreq;
  
/*
  unsigned long dur = (millis() - tic);
  if ( index == 0 ) {
    Serial << F("Last FFT complete.");
    Serial << F(" duration=") << dur;
    Serial << F(" ms.") << endl;
  }
  */
}
void PrintVector(double *vData, uint16_t bufferSize, uint8_t scaleType) {
  for (uint16_t i = 0; i < bufferSize; i++)   {
    double abscissa;
    /* Print abscissa value */
    switch (scaleType)
    {
      case SCL_INDEX:
        abscissa = (i * 1.0);
        break;
      case SCL_TIME:
        abscissa = ((i * 1.0) / DISTANCE_SAMPLING_FREQ);
        break;
      case SCL_FREQUENCY:
        abscissa = ((i * 1.0 * DISTANCE_SAMPLING_FREQ) / (double)N_FREQ_SAMPLES);
        break;
    }
    Serial.print(abscissa, 6);
    Serial.print(" ");
    Serial.print(vData[i], 4);
    Serial.println();

    // Only the first half of the output bins represent usable frequency values.
    if ( scaleType == SCL_FREQUENCY && i >= (bufferSize / 2 - 1) ) return;
  }
  Serial.println();
}
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

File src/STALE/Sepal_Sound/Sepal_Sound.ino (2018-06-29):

// IDE Settings:
// Tools->Board : "WeMos D1 R2 & mini"
// Tools->Flash Size : "4M (3M SPIFFS)"
// Tools->CPU Frequency : "160 MHz"
// Tools->Upload Speed : "921600"

#include <Streaming.h>
#include <Metro.h>
#include <SoftwareSerial.h>
#include <FiniteStateMachine.h>
#include <Tsunami.h>
#include "Nyctinasty_Messages.h"
#include "Nyctinasty_Comms.h"

// spammy?
#define SHOW_SERIAL_DEBUG true

// my role and arch number
NyctRole myRole = Sound; // see Nyctinasty_Comms.h; set N_ROLES to pull from EEPROM

// wire it up
// RX/TX for softserial comms
#define RX D1 // GPIO5.  wire to Tsunami TX0
#define TX D2 // GPIO4.  wire to Tsunami RX1
// talk to the Sound device device
SoftwareSerial mySerial(RX, TX, false, 1024);

// also used
// D4, GPIO2, BUILTIN_LED
#define LED BUILTIN_LED // our LED

// comms
NyctComms comms;

// define a state for every systemState
void startup(); State Startup = State(startup);
void offline(); State Offline = State(offline);
void online(); State Online = State(online);
void slaved(); State Slaved = State(slaved);

// Gameplay states
void idleEnter(); void idle(); void idleExit(); State Idle = State(idleEnter,idle,idleExit);
void introEnter(); void introExit(); State Intro = State(introEnter,NULL,introExit);
void coor1();  State Coor1 = State(coor1);
void coor2();  State Coor2 = State(coor2);
void coor3();  State Coor3 = State(coor3);
void win(); State Win = State(win);

// Sounds
#define IDLE_START 100
#define INTRO_START 200
#define WIN_START 300
#define C1_START 400
#define C2_START 500
#define C3_START 600

#define IDLE_NUM 8
#define INTRO_NUM 4
#define WIN_NUM 4
#define C1_NUM 1
#define C2_NUM 1
#define C3_NUM 1

#define IDLE_TIME 20000l
#define IDLE_PLAY_SPACING 4000l

Metro idleTimer(1UL);
Metro introLockoutTimer(1UL);



void reboot() {
  comms.reboot();
}; State Reboot = State(reboot);
void reprogram() {
  comms.reprogram("Sepal_Sound.ino.bin");
}; State Reprogram = State(reprogram);
FSM stateMachine = FSM(Startup); // initialize state machine

// incoming message storage and flag for update
struct sC_t {
  boolean hasUpdate = false;
  SystemCommand settings;
} sC;

// distance updates receive as this structure as this topic
typedef struct {
  boolean hasUpdate = false;
  SepalArchDistance dist;
} sAD_t;
sAD_t sAD[N_ARCH];

// frequency updates receive as this structure as this topic
typedef struct {
  boolean hasUpdate = false;
  SepalArchFrequency freq;
} sAF_t;
sAF_t sAF[N_ARCH];

// there will be a correspondence structure getting sent.  just don't know what it is, yet.

// Our Tsunami object
Tsunami tsunami;

// some tracks to mess with
const int BOOTS = 17;
const int SPARKLE = 18;
const int CATS = 19;

long lastActivity = 0;  // Last time we detected movement

void setup() {
  // for local output
  Serial.begin(115200);
  Serial << endl << endl << endl << F("Startup begins.") << endl;

  delay(1000);

  // for remote output
  Serial << F("Configure Tsunami...");
  // Tsunami startup at 57600
  tsunami.start();
  delay(10);

  // Send a stop-all command and reset the sample-rate offset, in case we have
  //  reset while the Tsunami was already playing.
  tsunami.stopAllTracks();
  tsunami.samplerateOffset(0, 0);

  // Enable track reporting from the Tsunami
  tsunami.setReporting(true);

  Serial << F(" done.") << endl;

  delay(1000);

  // configure comms
  comms.begin(myRole);
  myRole = comms.getRole();

  // subscribe
  comms.subscribe(&sC.settings, &sC.hasUpdate);
  for ( byte i = 0; i < N_ARCH; i++ ) {
    Serial.printf("Subscribe to arch: %d\n",i);
    // subscribe to frequency and distance messages
    comms.subscribe(&sAF[i].freq, &sAF[i].hasUpdate, i);
    comms.subscribe(&sAD[i].dist, &sAD[i].hasUpdate, i);
  }

  Serial << F("Setup complete. Wait for subscriptions") << endl;
/*
  long start = millis();
  while(millis() - start < 5000) {
    delay(10);
    comms.update();
  }
*/
  Serial << "Done with Setup" << endl;
  // Allow time for subscriptions to land
  //delay(5000);  // Not sure if this is really necessary but we dont always connect 

/*
  // run through some calculations to explain what's in the SepalArchFrequency data item.
  Serial << F("Actual frequencies in each power bin:") << endl;
  for(byte j=0; j<N_FREQ_BINS; j++) {
    Serial << F("Bin=") << j;
    Serial << F("\tFreq=") << ((float)j+1.0)*(float)DISTANCE_SAMPLING_FREQ/(float)N_FREQ_SAMPLES;
    Serial << endl;
  }
*/
}

void loop() {
  // comms handling
  comms.update();
  tsunami.update();


  // check for settings update
  if ( sC.hasUpdate ) {
    switchState(sC.settings.state);
    sC.hasUpdate = false;
  }

  // do stuff
  stateMachine.update();

  //mimicController();  // Uncomment to mimic the controller
  testStates();  // Uncomment to run through all the states
  
  // TODO: Add small delay here to allow interrupts to fire?
  delay(1);
}

void switchState(systemState state) {
  Serial << F("State.  Changing to ") << state << endl;
  switch ( state ) {
    case STARTUP: stateMachine.transitionTo(Startup); break;
    case OFFLINE: stateMachine.transitionTo(Offline); break;
    case ONLINE: stateMachine.transitionTo(Online); break;
    case SLAVED: stateMachine.transitionTo(Slaved); break;
    case REBOOT: stateMachine.transitionTo(Reboot); break;
    case REPROGRAM: stateMachine.transitionTo(Reprogram); break;
    
    case IDLE: stateMachine.transitionTo(Idle); break;
    case INTRO: stateMachine.transitionTo(Intro); break;
    case C1: stateMachine.transitionTo(Coor1); break;
    case C2: stateMachine.transitionTo(Coor2); break;
    case C3: stateMachine.transitionTo(Coor3); break;
    case WIN: stateMachine.transitionTo(Win); break;
    default:
      Serial << F("ERROR!  unknown state.") << endl;
  }
}

// Test states by running through each
void testStates() {
  static Metro stateChange(15000UL);

  if (!stateChange.check()) return;

  Serial << "Changing test state" << endl;
  
  if (stateMachine.isInState(Online)) {
    Serial << "Changing to Idle" << endl;
    stateMachine.transitionTo(Idle);
  }
  
  if (stateMachine.isInState(Idle)) {
    Serial << "Changing to Intro" << endl;
    stateMachine.transitionTo(Intro);
  }

  if (stateMachine.isInState(Intro)) {
    Serial << "Changing to Coor1" << endl;
    stateMachine.transitionTo(Coor1);
  }

  if (stateMachine.isInState(Coor1)) {
    Serial << "Changing to Coor2" << endl;
    stateMachine.transitionTo(Coor2);
  }

  if (stateMachine.isInState(Coor2)) {
    Serial << "Changing to Coor3" << endl;
    stateMachine.transitionTo(Coor3);
  }

  if (stateMachine.isInState(Coor3)) {
    Serial << "Changing to Win" << endl;
    stateMachine.transitionTo(Win);
  }

  if (stateMachine.isInState(Win)) {
    Serial << "Changing to Idle" << endl;
    stateMachine.transitionTo(Idle);
  }

  stateChange.reset();
}
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

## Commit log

2017-08-24 stubbed out Sensor, Light, MIDI
2017-08-24 touch-up to Sensor and Light
2017-08-26 src/Sensor should spew MQTT values
2017-08-26 Light moved to Comms framework
2017-08-27 prototype up
2017-08-28 Added sensor viz. Requires processing 3+
2017-08-28 comments on SensorViz.pde
2017-09-03 added datasheets and library for 850nm IR sensors
    [IR_sensor_distance_vs_Voltage.csv]
2017-09-10 Fixed reset pin. Reduced max network packet to 64 bytes to spend transmital
    [ContinuousDuo.ino, Sensor.ino]
2017-09-17 moved to 12bit ADC by oversampling on the Nano
2017-09-26 Basic midi prototype done
2017-09-26 Don't initialize broken sensor
    [Sensor.ino]
2017-09-26 Sharp IR sensors added
2017-10-01 Sharp IR has proper range calculation
    [IR_sensor_distance_vs_Voltage.csv]
2017-10-05 Added multiple sensor support
2017-11-02 tinkered with ADC device
2017-11-09 sharp sensors working
2017-11-12 ADC is working well
2017-12-08 should have a working system
    [Data.xlsx]
2017-12-12 dammit esp32 and your not working adc2
    [Sepal_Arch_Light.ino, Sepal_Coordinator.ino]
2017-12-18 working comms
    [data.csv]
2017-12-28 first push prototype
2018-01-02 processing script added.
    [scan-the-world-michelangelo-s-david - reduced.obj]
2018-01-04 processing 3D looks good
    [center - reduced.obj, sail_A rev 3.DXF, sail_B rev 3.DXF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]
2018-01-04 refined 3d model
    [center - reduced.obj, scan-the-world-michelangelo-s-david - reduced.obj]
2018-01-05 added lighting and sensor animations
2018-01-19 processing sketchs and a variety of stand-alone modules added
    [D1MSHO.brd, D1MSHO.sch, NodeArch.brd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]
2018-01-29 pumps added. weighted correlation added
2018-04-20 Arch board v3
    [NodeArch_v3.brd, NodeArch_v3.sch]
2018-05-14 production boards look good
2018-05-26 10 Hz distance data too
2018-06-01 Adjusted for six sensors
2018-06-08 Pumps stubbed
2018-06-14 made the offline pump shutdown stupider
2018-06-20 Coordinator dumping data
    [data_17Jun18.csv]
2018-06-26 Coordinator built out with game states
    [data_23Jun18.csv, truth_table_23Jun18 - edited.csv, truth_table_23Jun18.csv]
2018-07-02 new coordination data; moving to magister branch to test
    [data_30Jun18.csv, truth_table_23Jun18.csv]

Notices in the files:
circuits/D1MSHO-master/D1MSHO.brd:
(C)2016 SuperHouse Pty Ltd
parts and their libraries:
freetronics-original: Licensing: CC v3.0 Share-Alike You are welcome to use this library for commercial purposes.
